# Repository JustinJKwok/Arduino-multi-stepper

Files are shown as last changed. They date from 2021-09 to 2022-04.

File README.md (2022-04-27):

# Arduino-multi-stepper
Control multiple stepper motors using an arduino.

### Table of Contents
1. [Getting Started](#getting-started)
    - [Requirements](#requirements)
    - [Setup and Installation](#setup-and-installation)
        - [Stepper Driver Setup](#stepper-driver-setup)
2. [Usage](#usage)
    - [Commands](#commands)
3. [Materials](#materials)
4. [Wiring Scheme](#wiring-scheme)
    - [PCB](#pcb)
5. [License](#license)

## Getting Started
### Requirements
The following arduino libraries are used:
- AccelStepper
  
### Setup and Installation
Make relevant modifications and upload the sketch to your arduino.

Here's what you may need to modify (for each motor) based on your specific application:
- Pin assignments (for stepper drivers and limit switches)
- The following are coded in, but are planned to be changeable with commands:
  - (max)MotorSpeed
  - (max)MotorAccel
- stepsPerRev, steps per revolution (e.g. 1/8 microstepping on a 1.8 deg (200 step) motor is 1600 steps)
- distPerRev, distance per revolution for your motion system. (e.g. motor directly coupled to a 2 mm pitch/4 start lead screw = 8 mm distance per rev)
  - if you are using your stepper for a purpose other than linear motion, then have the 'distance' be in whatever units of what you are actually doing. For example, for a rotating/angular positioning system, 'distance' would be in units of degrees or radians.
- min and maxPosition
  - As above, have the 'position' be in whatever units you are using. For a rotational system this would be a min and max angle.  
- isForwardCCW, whether counter clock-wise (looking from motor to shaft end) is considered forward (positive) motion. (May be reversed for you stepper driver)
- disableWhenStill, depower the motor when not moving. Steppers generate heat when actively holding position. This will disable that but the motor can be turned by an external force (which may be desirable in some cases).
- setPinsInverted arguments in setup(), this depends on your stepper driver.
- Serial baudrate

#### Stepper Driver Setup
This project uses the TMC2209 SilentStepStick which is a drop-in replacement for the common A4988 driver. You may need to change the setPinsInverted arguments depending on your stepper driver.

Regardless of your driver, you will need to set the motor current by adjusting a potentiometer on the driver board. This depends on both your driver and stepper motor specs. Depending on your current setting you may also need to apply a heatsink to your driver.

## Usage
The arduino parses its serial buffer for commands. If the command is valid it then executes it. 
To send commands you will need to connect the arduino to a usb port and use a program like Arduino Serial Monitor or PuTTY to send commands.
Each command must have a header and foot character to indicate the beginning and end of your message. By default these are ">" and "\n", respectively, but can be changed.
For a list of commands see below. The arduino can also report relevant info like current position and when a move is completed.

Instead of sending manual commands like above, you can automate the device or use it as part of a larger program. This can be done for example with PySerial.
A Python module for controlling this specific arduino stepper controller and using it in combination with other devices for lab automation is available here:

[Lab Automation](https://github.com/JustinJKwok/LabAutomation)

If you want to develop your own software package then the communication protocol is as follows:

Host sends a command to the arduino:

- If the command is valid, the arduino responds "ACK" + and optional message
- If the command is invalid, the arduino responds "NAK  + and optional message

If the command is valid, then the arduino proceeds to execute the command.
- If the action was performed successfully, the arduino responds with "SUCC"  + and optional message
- If the action encountered a problem, the arduino responds with "FAIL"  + and optional message.

The arduino response characters can be changed in the sketch to any char(s) or byte(s) you want, such as "\x06" for ACK.

### Commands

To add all commands and descriptions here

## Materials
Current design uses 2 NEMA 17 stepper motors but is generalizable to 1 stepper or many more steppers. You can add more steppers as long as you have appropriate power supply.

Here are the materials you will need. The specific components I used are indicated in parenthesis.
- Arduino microcontroller (Uno)
- Stepper motor(s), 4 wire bipolar (stepperonline NEMA 17, s/n: 17HS08-1004S)
- Stepper driver per motor (TMC2209 SilentStepStick)
- Limit switch for homing per motor, normally closed (ServoCity Micro Limit Switch (Bump Lever))
- Pull-down resistors for limit switches (10kOhm)
- Decoupling capacitor for stepper driver Vm and Gnd (100 uF, this is well documented online)
- Schottky diodes (for [SilentStepSticks with variable 3-5V logic voltage](https://learn.watterott.com/silentstepstick/pinconfig/))
- Power supply for the stepper motors, 12V+ (this is not the voltage rating of your stepper, use 12V atleast with sufficient current)
  - A stepper motor still draws current when it is not moving, so keep this in mind when sizing systems with multiple steppers.
- Logic power supply, 5V
  - You can use a regulator or buck converter to step down your motor supply voltage. (I used a DFR0571 buck converter).

## Wiring Scheme
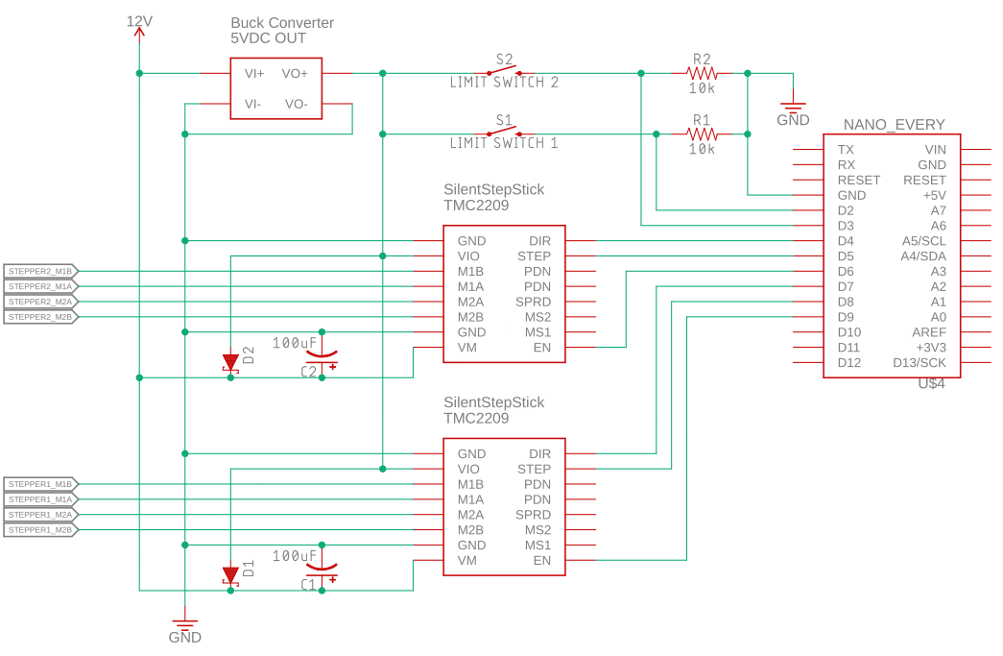
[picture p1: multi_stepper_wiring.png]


### PCB
Gerber files of a PCB for controlling 4 steppers is included. JST-XH connectors are intended for the motor and limit switches. Motor power comes from voltage supplied through a DC barrel which is also regulated down for 5V logic supply. 5V jumper pads are available for each driver's MS1, MS2, MS3 pins. A connection for an optional I2C LCD display is also provided. 4 mounting holes are provided with diameters of 0.138'' or 3.5 mm.

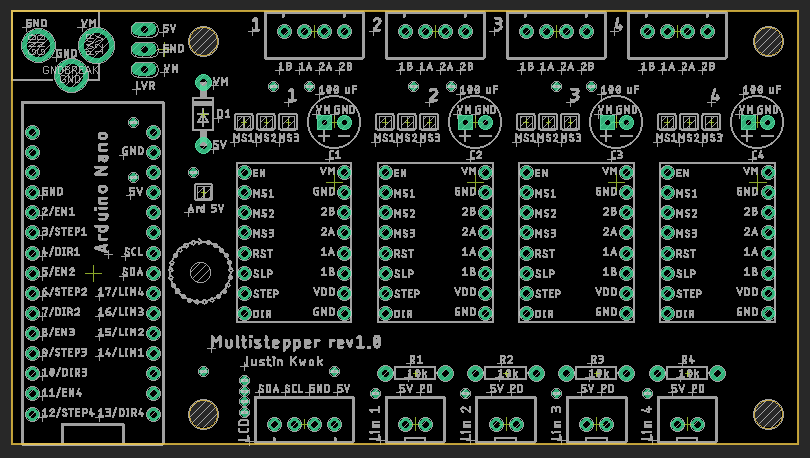
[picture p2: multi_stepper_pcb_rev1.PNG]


## License
To add

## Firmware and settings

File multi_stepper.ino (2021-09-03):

#include <AccelStepper.h>

#define M1_EN_PIN 7
#define M1_STEP_PIN 8
#define M1_DIR_PIN 9

#define M2_EN_PIN 4
#define M2_STEP_PIN 5
#define M2_DIR_PIN 6

int homeSwitchPin[] = {2, 3};

const int numSteppers = 2;
AccelStepper stepper1 = AccelStepper(stepper1.DRIVER, M1_STEP_PIN, M1_DIR_PIN);
AccelStepper stepper2 = AccelStepper(stepper2.DRIVER, M2_STEP_PIN, M2_DIR_PIN);
AccelStepper* steppers[numSteppers] = {&stepper1, &stepper2}; 
//for multiple steppers see https://forum.arduino.cc/t/solved-accelstepper-library-and-multiple-stepper-motors/379416/2

// each element corresponds to a stepper motor
float maxMotorSpeed[] = {0.5, 0.5}; //units of rev per sec
float maxMotorAccel[] = {1.0, 1.0}; //units of rev per sec per sec
float stepsPerRev[] = {1600.0, 1600.0}; // 1/8 microstepping
float distPerRev[] = {8.0, 8.0}; // 2 mm pitch w/ 4 start lead screw = 8 mm lead (or 8 mm traveled per lead screw revolution)
float homingBuffer[] = {5.0, 5.0}; //units: mm. how much to move forward after triggering homing/limit switch.
float minPosition[] = {0.0, 0.0};
float maxPosition[] = {80.0, 80.0};
bool isForwardCCW[] = {true, true}; //determines which direction is forward or positive
bool hasHomed[] = {false, false};
bool isHoming[] = {false, false};
bool hasReported[] = {true, true};
bool disableWhenStill[] = {true, true};

float stepsPerDist[numSteppers];

// see Serial Input Basics by Robin2: https://forum.arduino.cc/t/serial-input-basics-updated/382007/2
const int maxChars = 32; //max number of chars when reading from serial into cstring. anything larger rewrites last char of cstring (?)
const int maxTokens = 10; //max number of "words" or "tokens" separated by spaces (e.g. "mv samx 1" is 3 words or 3 tokens). print error if exceeded
char incomingChars[maxChars]; //incoming chars until newline terminator
char incomingParams[maxTokens][maxChars]; //incoming chars parsed into cstrings
char tempChars[maxChars];
bool newSerialData = false; // whether there is new data parsed from serial that needs to be processed
int numTokens = 0; //number of tokens or params
//strtoX endptr https://stackoverflow.com/questions/27973759/return-value-of-strtod-if-string-equals-to-zero

char charACK[] = "ACK"; //"\x06";
char charNAK[] = "NAK";
char charSUCC[] = "SUCC";
char charFAIL[] = "FAIL";
char charWARN[] = "WARN";

bool isDebugging = false;

//----------SETUP----------
void setup() 
{
    //initialize stepper params
    //tmc2209 silentstepstick stepper driver in standalone/legacy mode
    steppers[0]->setEnablePin(M1_EN_PIN);
    steppers[1]->setEnablePin(M2_EN_PIN);
    
    for (int i = 0; i < numSteppers; ++i)
    {
        stepsPerDist[i] = stepsPerRev[i] / distPerRev[i];
        
        pinMode(homeSwitchPin[i], INPUT);
  
        steppers[i]->setPinsInverted(isForwardCCW[i], false, true); 
        //dir, step, enable. if dir not inverted, then +'ve step produces lead screw rotation clockwise (looking from motor to end) and carriage moves towards the motor
        
        steppers[i]->enableOutputs();
        steppers[i]->setAcceleration(stepsPerRev[i] * maxMotorAccel[i]);
        steppers[i]->setMaxSpeed(stepsPerRev[i] * maxMotorSpeed[i]);
        steppers[i]->setSpeed(stepsPerRev[i] * maxMotorSpeed[i]);
        steppers[i]->setCurrentPosition(0);

        if (disableWhenStill[i])
        {
            steppers[i]->disableOutputs();
        }
    }

    Serial.begin(115200);
}

void loop() 
{
    readNextSerial();

    //Process new parsed commands
    if (newSerialData == true)
    {
        if (isDebugging)
        {
            Serial.print(">>");
            Serial.println(incomingChars);
        }

        strcpy(tempChars, incomingChars);
        parseTokens();
        goToCommand();
    }

    //run stepper motors
    for (int i = 0; i < numSteppers; ++i)
    {
      // if currently homing and the limit switch is depressed
      if (isHoming[i] && !digitalRead(homeSwitchPin[i]))
      {
            steppers[i]->enableOutputs();
            steppers[i]->move(homingBuffer[i] * stepsPerDist[i]);
            hasReported[i] = false;   
      }
      
      if (steppers[i]->distanceToGo() != 0)
      {
          // can this cause intervals to skip? because not EXACTLY a multiple of 100 on evaluation
          // might depend on how slow/fast the main loop is, if too fast then it will repeat, if to slow it may skip
          // not too critical since only used for printing 
          if (millis() % 100 == 0 && isDebugging)
          {
              Serial.print("Moving, distance to go for stepper ");
              Serial.print(i+1);
              Serial.print(" is: ");
              Serial.print(steppers[i]->distanceToGo() / stepsPerDist[i]);
              Serial.print(" at ");
              Serial.println(steppers[i]->currentPosition() / stepsPerDist[i]);
          }
          steppers[i]->run();
      }
      else if (!hasReported[i])
      {
          if (isHoming[i])
          {
            steppers[i]->setCurrentPosition(0);
            isHoming[i] = false;
            hasHomed[i] = true;

            //Homing completion message
            printSUCC();
            Serial.print("Stepper ");
            Serial.print(i+1);
            Serial.println(" has been homed. Current position set to zero.");
            
          }
          else
          {
            //Regular move completion message
            printSUCC();
            Serial.print("Move complete for stepper  ");
            Serial.print(i+1);
            Serial.print(" at ");
            Serial.println(steppers[i]->currentPosition() / stepsPerDist[i]);
          }
           if (disableWhenStill[i])
          {
              steppers[i]->disableOutputs();
          }
          hasReported[i] = true;    
      }
      else if(hasReported[i] && isHoming[i])
      {
          isHoming[i] = false;
          hasHomed[i] = false;
          
          printFAIL();
          Serial.print(F("Did not hit limit switch when homing stepper "));
          Serial.print(i+1);
          Serial.println(F(". Stepper has not been homed. Inspect system and try again."));
      }
    }
   
    //reset new data flag
    newSerialData = false;
    //reset the parsed tokens
    for (int i = 0; i < numTokens; ++i)
    {
        incomingParams[i][0] = '\0';
    }
    //reset the token counter
    numTokens = 0;
}

//----------SERIAL AND UTILITY FUNCTIONS----------
void readNextSerial()
{
    //read serial buffer until newline, read into incomingChars
    static bool hasReadHeader = false;
    static int ndx = 0;
    char nextChar;
    char footer = '\n';
    char header = '>';

    while (Serial.available() > 0 && newSerialData == false)
    {
        nextChar = Serial.read();

        if (hasReadHeader == true)
        {
            //keep adding into cstring until newline
            if (nextChar != footer)
            {
                incomingChars[ndx] = nextChar;
                ++ndx;
                if (ndx >= maxChars)
                {
                    ndx = maxChars - 1;
                }
            }
            else
            {
                //if reading newline then terminate cstring and indicate there is new data to process
                incomingChars[ndx] = '\0';
                ndx = 0;
                newSerialData = true;
                hasReadHeader = false;
            }
        }
        else if (nextChar == header)
        {
            hasReadHeader = true;
        }
    }
}

void parseTokens()
{
    char* token;
    numTokens = 0;

    token = strtok(tempChars, " ");

    while (token != NULL)
    {
        //save into cstring array and read next portion
        strcpy(incomingParams[numTokens], token);
        ++numTokens;

        if (numTokens >= maxTokens)
        {
            numTokens = maxTokens - 1;
        }
        token = strtok(NULL, " ");
    }
}

bool isValidMotorNum(char* str, long& num)
{
    char* endptr;
    num = strtol(str, &endptr, 10);
    if (endptr == str || *endptr != '\0')
    {
        printNAK();
        Serial.print("Parameter ");
        Serial.print(str);
        Serial.println(" is not an integer");
        return false;
    }
    else
    {
        if (num <= 0 || num > numSteppers)
        {
            printNAK();
            Serial.println("Stepper number is invalid");
            return false;
        }
        else
        {
            return true;
        }
    }
}

bool isValidTargetPos(char* str, long motorNum, double& pos)
{
    char* endptr;
    pos = strtod(str, &endptr);
    if (endptr == str || *endptr != '\0')
    {
        printNAK();
        Serial.print("Parameter ");
        Serial.print(incomingParams[2]);
        Serial.println(" is not a number");
        return false;
    }
    else
    {
        if (pos < minPosition[motorNum-1] || pos > maxPosition[motorNum-1])
        {
            printNAK();
            Serial.print("Position ");
            Serial.print(pos);
            Serial.println(" is out of range");
            return false;
        }
        else
        {
          return true;
        }
    }
}

bool isValidRelativeDist(char* str, long motorNum, double& dist, double& pos)
{
    char* endptr;
    dist = strtod(str, &endptr);
    if (endptr == str || *endptr != '\0')
    {
        printNAK();
        Serial.print("Parameter ");
        Serial.print(incomingParams[2]);
        Serial.println(" is not a number");
        return false;
    }
    else
    {
        pos = steppers[motorNum-1]->currentPosition() / stepsPerDist[motorNum-1] + dist;
        if (pos < minPosition[motorNum-1] || pos > maxPosition[motorNum-1])
        {
            printNAK();
            Serial.print("Position ");
            Serial.print(pos);
            Serial.println(" is out of range");
            return false;
        }
        else
        {
          return true;
        }
    }
}

//---------COMMAND FUNCTIONS------------
void homeMotor()
{
    if (numTokens == 1)
    {
        printlnACK();
        for (int i = 0; i < numSteppers; ++i)
        {
            double distance = maxPosition[i] - minPosition[i] + homingBuffer[i] + 2.0;
            steppers[i]->enableOutputs();
            steppers[i]->move(-1.0*distance * stepsPerDist[i]);
            isHoming[i] = true;
        }
    }
    else if (numTokens == 2)
    {
        long motorNum;
        if (!isValidMotorNum(incomingParams[1], motorNum))
        {
            return;
        }

        printlnACK();
        double distance = maxPosition[motorNum-1] - minPosition[motorNum-1] + homingBuffer[motorNum-1] + 2.0;
        steppers[motorNum-1]->enableOutputs();
        steppers[motorNum-1]->move(-1.0*distance * stepsPerDist[motorNum-1]);
        isHoming[motorNum-1] = true;
    }
    else
    {
        printNAK();
        Serial.println("Invalid number of parameters");
    }
}

void unhomeMotor()
{
    if (numTokens == 1)
    {
        printlnACK();
        for (int i = 0; i < numSteppers; ++i)
        {
            steppers[i]->stop();
            steppers[i]->disableOutputs();
            isHoming[i] = false;
            hasHomed[i] = false;
        }
        printSUCC();
        Serial.println("Flagging all motors as not homed");
    }
    else if (numTokens == 2)
    {
        long motorNum;
        if (!isValidMotorNum(incomingParams[1], motorNum))
        {
            return;
        }

        printlnACK();

        steppers[motorNum-1]->stop();
        steppers[motorNum-1]->disableOutputs();
        isHoming[motorNum-1] = false;
        hasHomed[motorNum-1] = false;

        printSUCC();
        Serial.print("Flagging stepper ");
        Serial.print(motorNum);
        Serial.println(" as not homed");
    }
    else
    {
        printNAK();
        Serial.println("Invalid number of parameters");
    }
}

void moveAbsolute()
{
    //Check the number of tokens
    if (numTokens != 3)
    {
        printNAK();
        Serial.println("Invalid number of parameters");
        return;
    }

    //Check that the first number is an integer and is within the range of valid stepper numbers
    long motorNum;
    if (!isValidMotorNum(incomingParams[1], motorNum))
    {
        return;
    }
    
    //Check that the second number is an actual number and is within the range of valid positons
    double targetPos;
    if (!isValidTargetPos(incomingParams[2], motorNum, targetPos))
    {
        return;
    }

    printlnACK();

    if (!hasHomed[motorNum-1])
    {
        printFAIL();
        Serial.print("You must home stepper ");
        Serial.print(motorNum);
        Serial.println(" before you can move it");
        return;
    }

    //Successful 
    if (isDebugging)
    {
        Serial.print("Moving stepper ");
        Serial.print(motorNum);
        Serial.print(" to ");
        Serial.println(targetPos);
    }
    //enable and disable outputs when not moving in future
    steppers[motorNum-1]->enableOutputs();
    steppers[motorNum-1]->moveTo(targetPos * stepsPerDist[motorNum-1]);
    hasReported[motorNum-1] = false;
    
}

void moveRelative()
{
    //Check the number of tokens
    if (numTokens != 3)
    {
        printNAK();
        Serial.println("Invalid number of parameters");
        return;
    }

    //Check that the first number is an integer and is within the range of valid stepper numbers
    long motorNum;
    if (!isValidMotorNum(incomingParams[1], motorNum))
    {
        return;
    }

    //Check that the second number is an actual number and is within the range of valid positons
    double distance;
    double targetPos;
    if (!isValidRelativeDist(incomingParams[2], motorNum, distance, targetPos))
    {
        return;
    }  

    printlnACK();

    if (!hasHomed[motorNum-1])
    {
        printFAIL();
        Serial.print("You must home stepper ");
        Serial.print(motorNum);
        Serial.println(" before you can move it");
        return;
    }

    //Successful 
    if (isDebugging)
    {
        Serial.print("Moving stepper ");
        Serial.print(motorNum);
        Serial.print(" by ");
        Serial.print(distance);
        Serial.print(" to ");
        Serial.println(targetPos);
    }

    //enable and disable outputs when not moving in future
    steppers[motorNum-1]->enableOutputs();
    steppers[motorNum-1]->moveTo(targetPos * stepsPerDist[motorNum-1]);
    //steppers[motorNum-1]->move(distance * stepsPerDist[motorNum-1]); //same as above
    hasReported[motorNum-1] = false;
}

//void setPosition()
//{
//    //dont make available to the user.
//    Serial.println("Reset position command");
//}

void stopMotor()
{
    //WARNING stop will send ACK/NAK and SUCC if already stopped (main loop will send SUCC if moving then stopping)
    //BUT if the motor is already moving a SUCC/FAIL is expected for that command and calling stop will mess up the expected flow control by 
    //interjecting an additional ACK/NAK before reporting completion/stop with SUCC/FAIL
    //In other words, this is fine for manual control or emergency stops but not for automation when specific protocol is expected from the host
    if (numTokens == 1)
    {
        printlnACK();
        if (isDebugging)
        {
            Serial.println(F("Stopping all stepper motors"));
        }
        for (int i = 0; i < numSteppers; ++i)
        {
            steppers[i]->stop();

            if (steppers[i]->distanceToGo() == 0)
            {
                printSUCC();
                Serial.print("Stepper ");
                Serial.print(i+1);
                Serial.println(" is already stopped");
            }
            //if stepper is moving then SUCC will be sent when reporting completion
        }
    }
    else if (numTokens == 2)
    {
        long motorNum;
        if (!isValidMotorNum(incomingParams[1], motorNum))
        {
            return;
        }

        printlnACK();

        if (isDebugging)
        {
            Serial.print("Stopping stepper ");
            Serial.println(motorNum);
        }
        
        steppers[motorNum-1]->stop();

        if (steppers[motorNum-1]->distanceToGo() == 0)
        {
            printSUCC();
            Serial.print("Stepper ");
            Serial.print(motorNum);
            Serial.println(" is already stopped");
        }
        //if stepper is moving then SUCC will be sent when reporting completion
    }
    else
    {
        Serial.println("Invalid number of parameters");
    }
}

void whereMotor()
{
    if (numTokens == 1)
    {
      printlnACK();
      for (int i = 0; i < numSteppers; ++i)
      {
         printSUCC();
         Serial.print("Stepper ");
         Serial.print(i+1);
         Serial.print(" is at = ");
         Serial.println(steppers[i]->currentPosition() / stepsPerDist[i]);
      }
    }
    else if (numTokens == 2)
    {
        long motorNum;
        if (!isValidMotorNum(incomingParams[1], motorNum))
        {
            return;
        }

        printlnACK();
        printSUCC();
        Serial.print("Stepper ");
        Serial.print(motorNum);
        Serial.print(" is at = ");
        Serial.println(steppers[motorNum-1]->currentPosition() / stepsPerDist[motorNum-1]);
    }
    else
    {
        printNAK();
        Serial.println("Invalid number of parameters");
    }
}

void enableMotor()
{
    if (numTokens == 1)
    {
        printlnACK();
        if (isDebugging)
        {
            Serial.println(F("Enabling all stepper motors"));
        }
        for (int i = 0; i < numSteppers; ++i)
        {
            steppers[i]->stop();
            steppers[i]->enableOutputs();
        }
        printSUCC();
        Serial.println(F("Steppers have been enabled"));
    }
    else if (numTokens == 2)
    {
        long motorNum;
        if (!isValidMotorNum(incomingParams[1], motorNum))
        {
            return;
        }

        printlnACK();

        if (isDebugging)
        {
            Serial.print("Enabling stepper ");
            Serial.println(motorNum);
        }

        steppers[motorNum-1]->stop();
        steppers[motorNum-1]->enableOutputs();

        printSUCC();
        Serial.print("Stepper ");
        Serial.print(motorNum);
        Serial.println(" has been enabled");
    }
    else
    {
        printNAK();
        Serial.println("Invalid number of parameters");
    }
}

void disableMotor()
{
    if (numTokens == 1)
    {
        printlnACK();

        if (isDebugging)
        {
            Serial.println(F("Disabling all stepper motors"));
        }
        for (int i = 0; i < numSteppers; ++i)
        {
            steppers[i]->stop();
            steppers[i]->disableOutputs();
        }
        printSUCC();
        Serial.println(F("Steppers have been disabled"));
    }
    else if (numTokens == 2)
    {
        long motorNum;
        if (!isValidMotorNum(incomingParams[1], motorNum))
        {
            return;
        }

        printlnACK();

        if (isDebugging)
        {
            Serial.print("Disabling stepper ");
            Serial.println(motorNum);
        }

        steppers[motorNum-1]->stop();
        steppers[motorNum-1]->disableOutputs();

        printSUCC();
        Serial.print("Stepper ");
        Serial.print(motorNum);
        Serial.println(" has been disabled");
    }
    else
    {
        printNAK();
        Serial.println("Invalid number of parameters");
    }
}

void setDebugOn()
{
    if (numTokens == 1)
    {
        isDebugging = true;
        Serial.println(F("Debug messages turned ON"));
    }
    else
    {
        if (isDebugging)  
        {
            Serial.println("Invalid number of parameters");
        }
    }
}

void setDebugOff()
{
    if (numTokens == 1)
    {
        isDebugging = false;
        //should not be able to print below if false
        //Serial.println("Debug messages turned OFF");
    }
    else
    {
        if (isDebugging)  
        {
            Serial.println("Invalid number of parameters");
        }
    }
}

void goToCommand()
{
    //Run function based on first parsed token
    //(cannot use switch/case for cstring comparisons, it is actually better with the if-else ladder in this particular situation)
    if (strcmp(incomingParams[0], "hm") == 0)
    {   
        homeMotor();
    }
    else if (strcmp(incomingParams[0], "unhm") == 0)
    {   
        unhomeMotor();
    }
    else if (strcmp(incomingParams[0], "mv") == 0)
    {   
        moveAbsolute();
    }
    else if (strcmp(incomingParams[0], "mvr") == 0)
    {
        moveRelative();
    }
    else if (strcmp(incomingParams[0], "set") == 0)
    {
        Serial.println(F("Resetting vars is not allowed for the user"));
        //setPosition();
    }
    else if (strcmp(incomingParams[0], "stop") == 0 || strcmp(incomingParams[0], "s") == 0)
    {
        stopMotor();
    }
    else if (strcmp(incomingParams[0], "wm") == 0)
    {
        whereMotor();
    }
    else if (strcmp(incomingParams[0], "enm") == 0)
    {
        enableMotor();
    }
    else if (strcmp(incomingParams[0], "dism") == 0)
    {
        disableMotor();
    }
    else if (strcmp(incomingParams[0], "debugon") == 0)
    {
        setDebugOn();
    }
    else if (strcmp(incomingParams[0], "debugoff") == 0)
    {
        setDebugOff();
    }
    else if (strcmp(incomingParams[0], "whoru") == 0)
    {
        printWhoAmI();
    }
    else if (strcmp(incomingParams[0], "help") == 0)
    {
        printHelp();
    }
    else if (strcmp(incomingParams[0], "info") == 0)
    {
        printMotorInfoCmd();
    }
    else if (strcmp(incomingParams[0], "") == 0)
    {
        //Serial.println("Blank token");
        //this happens if only header and footer are sent
    }
    else
    {
        //no command exists
        printNAK();
        Serial.print("No command \"");
        Serial.print(incomingParams[0]);
        Serial.println("\" exists. Type \"help\' for more info.");
    }
}

void printWhoAmI()
{
    Serial.println(F("This is an Arduino controller for stepper motors"));
}
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
